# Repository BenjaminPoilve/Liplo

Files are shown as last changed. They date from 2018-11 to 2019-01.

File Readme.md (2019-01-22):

# Liplo

> You can find an article about my adventures with plotters [here](https://www.benjaminpoilve.com/projects/plotter-story.html#)

An easy-to-assemble and fun-to-use pen plotter.

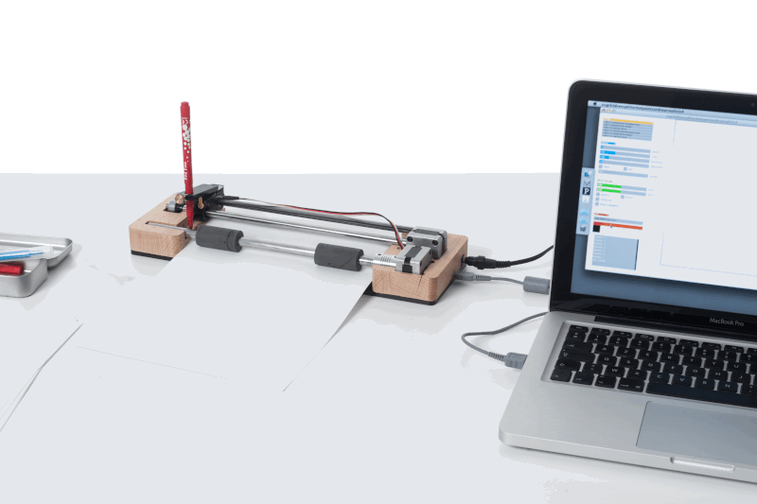
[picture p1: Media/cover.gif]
(https://www.youtube.com/watch?v=27pN25DA5TU&t=17s)


(click on the gif to have a video of all the iterations of Liplo)

The goal of this project is to imagine an easy to use and simple desktop printer, open to experimentations. Being able to use a wide array of tools (pen, pencil, brush) and paper types, it allows to really discover the world of CNC tools. Control of the printer can be done through a software that uses vector drawing, or through processing with the help of a simple software library, to discover generative drawing.

This is an old project of mine, I tried to make it a product (see my repo [LiploV2](https://github.com/BenjaminPoilve/LiploV2)) but I failed to manage the operational part of it. I put it on github in case it might inspire someone!

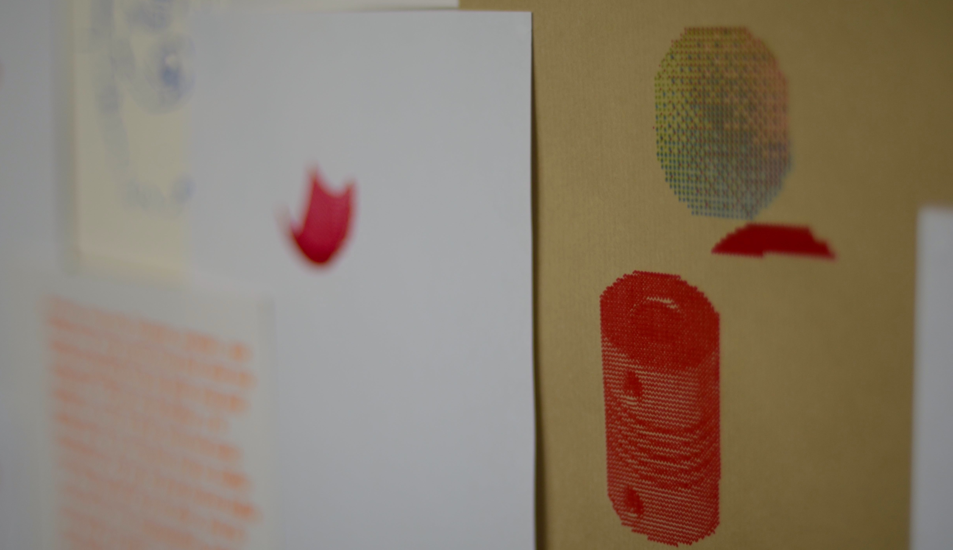
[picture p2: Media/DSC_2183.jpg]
Here

## The build

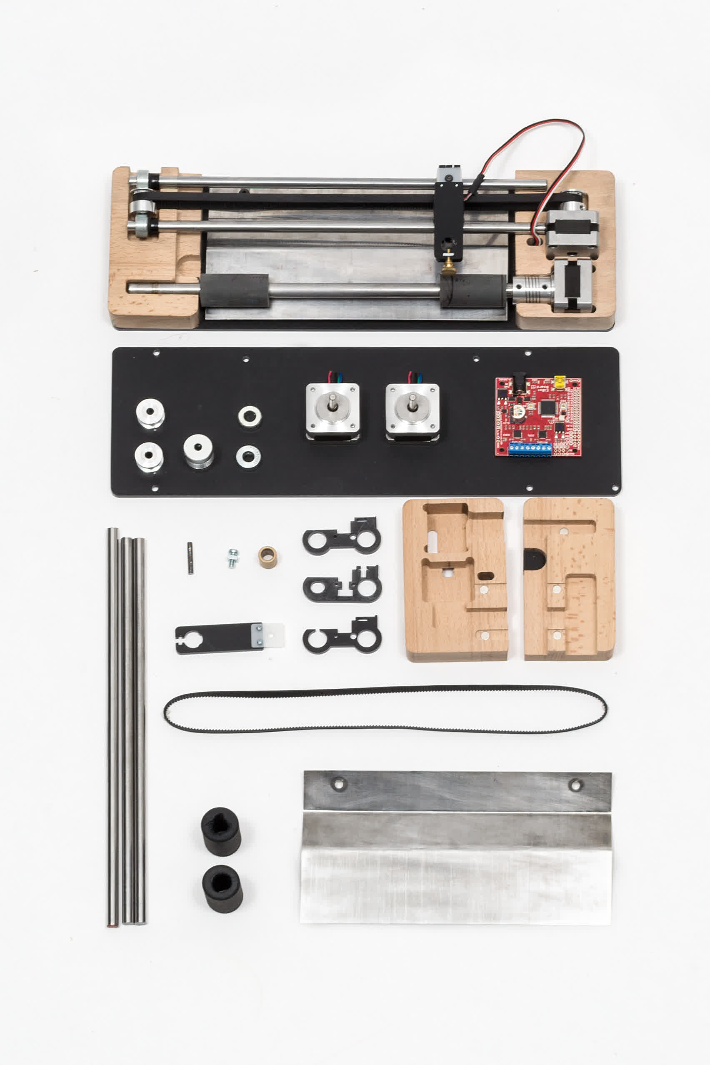
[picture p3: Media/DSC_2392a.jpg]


The construction is based on standard pieces. This allows the user to buy those pieces cheaply. 

The parts that need to be made are:

* Some laser cut parts for the head as well as the bottom of the machine
* Two CNC routed wood pieces
* A bended spring steel plate

The last one is the harder to manufacture. I did not find any manufacturer that made such parts. If you have an industrial metal bender at hand, this is pretty easy to do, but most people dont. This piece is used to maintain pressure between the paper and the roller.

On the electronic's side, I decided to use an [EibotBoard](http://www.schmalzhaus.com/EBB/). This is a very sturdy piece of hardware, that can be [bought](https://shop.evilmadscientist.com/productsmenu/188) quite cheaply. Both motor are Nema 14. I recommand [Robotdigg](https://www.robotdigg.com/) for most hardware purchase.

The last part of this project that is quite fun is that the axis are held in place only by magnet inserted in the wood. This allow for a very easy assembly.

#### B.O.M.

| Part | Approximate Price |  Link |
|---|:---:|:---:|
| EBB | $50 | [link](https://shop.evilmadscientist.com/productsmenu/188) |
| 2 Nema 14 Stepper 26mm |  $16.74|  [link](https://www.omc-stepperonline.com/nema-14-stepper-motor/nema-14-bipolar-18deg-14ncm-20ozin-04a-12v-35x35x26mm-4-wires-14hs10-0404s.html) |
| Power HD DS44 servomotor | $12 | |
| Acetal Copolymer hinge | $3.5 | [link](https://shop.evilmadscientist.com/partsmenu/200-hinges) |
| Wood | $10  | local seller  |
| Plexiglass |  $10  | local seller  |
| Flex Coupler | $1.50 |  [link](https://www.robotdigg.com/product/83/Flexible-Coupling-4mm,-5mm-Shaft-to-Screws) |
| 2 Pulley | $1.4| [link](https://www.robotdigg.com/product/226/20-Tooth-2GT-Pulley-10pcs-per-lot) |
| Linear Bearrings |  $.55 | [link](https://www.robotdigg.com/product/68/8mm-ID-Self-lubricating-Bearing)|
| GT2 Belt 6mm (not sure of length) | $1.05 | [link](https://www.robotdigg.com/product/275)|
| Tensioner| $0.15 | [link](https://www.robotdigg.com/product/41/Timing-Belt-Tensioner-Spring)|
| 2 8mm shaft collar| $0.5|  [link](https://www.robotdigg.com/product/750/DIY-motor-shaft-collar) |
| Stub 8mm| $10| local seller |
| Stub 10mm| $10 |  local seller |
| Polyurethane roller | $10 |  ebay |
| Neodyme Magnet 6mm*5mm |  $2.54 | [link](https://www.amazon.fr/Magnet-Expert-diam%C3%A8tre-n%C3%A9odyme-dadh%C3%A9rence/dp/B003MW8EJC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)|
| Spring Stell 3/10 | $5 | local seller  |
| 5*M3 screws | $1 | local seller |
| 3*M4 screws | $1 |  local seller  |
| 2 steel screws |  $1 |  local seller |

I might have forgotten a few parts but that is mostly it!

#### Laser cut parts

Two pieces are being cut in plexiglass with a laser cutter:

* The base 
* The head of the plotter

This part is inspired by Evil Mad scientist creations. This uses the same flexible hinge/servo association to lift the pen. 

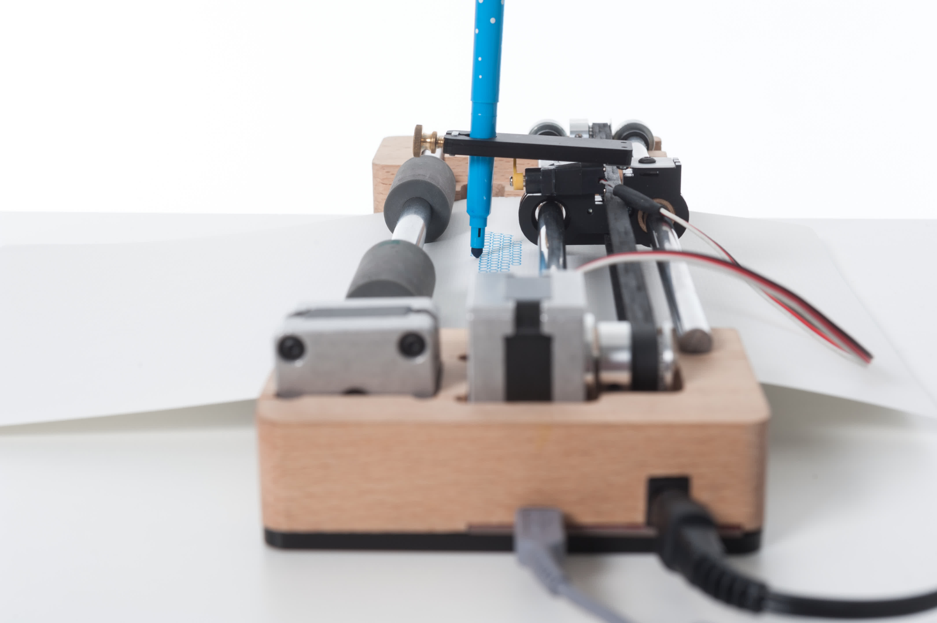
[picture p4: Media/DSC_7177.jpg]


There are three laser cut parts that assemble together and that clamp the timing belt. 

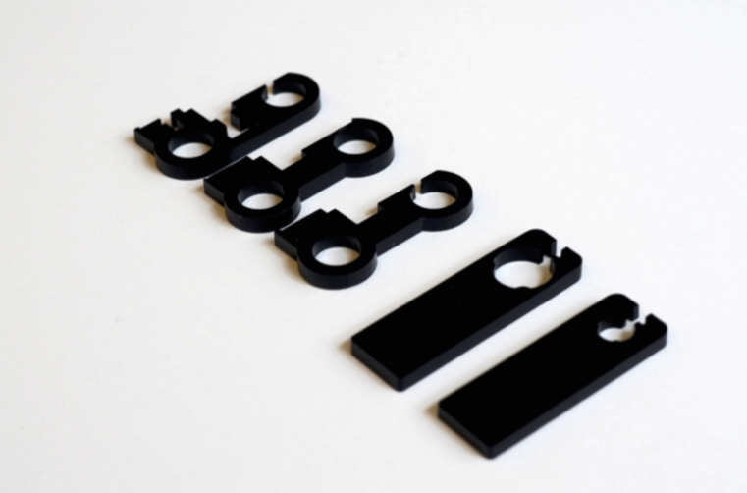
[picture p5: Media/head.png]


All the part can be cut from the same plexiglass stock.

See [here](Hardware/Plans/LaserCutParts)

#### CNC routed parts

For the routed parts, I choose to generate the gcode from a 2D drawing and not a 3D one. The goal was to have only one tool (6mm router head) for all the cutting, and to optimise the router path 

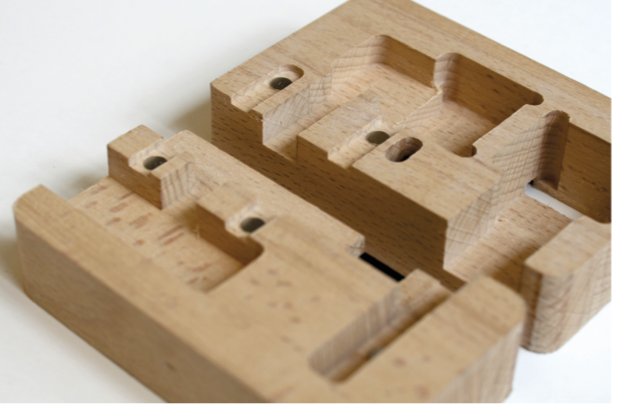
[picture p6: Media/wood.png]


What's more, since I did not have access to a very sophisticated router, I choose to use something that I call a flip cut to handle the part flip during routing.

The main idea is to have a border cut that allows the piece to be hold when the flip has been made.

It looks like this:

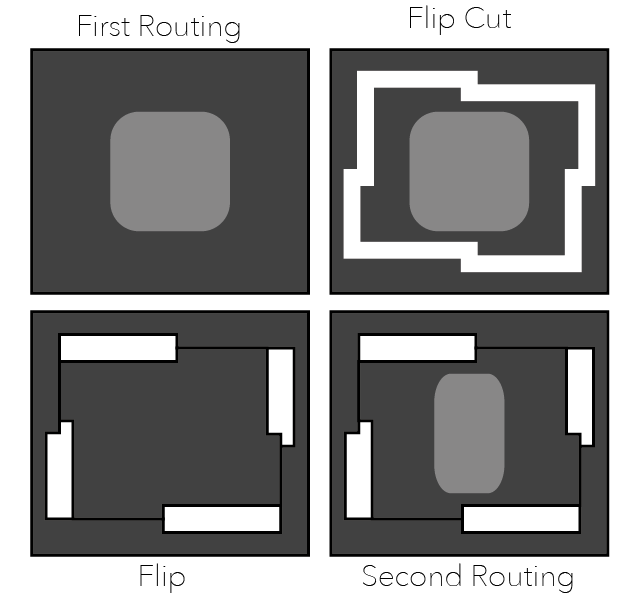
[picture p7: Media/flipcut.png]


You can find the G-code [here](Hardware/Plans/CNCparts) as well as the drawing you would need to regenerate the G-code.

## The software

The board itself already has an EibotFirmware.

Regarding the host computer, I made, using Processing (that was a long time ago!), a sender software.

#### Sender software

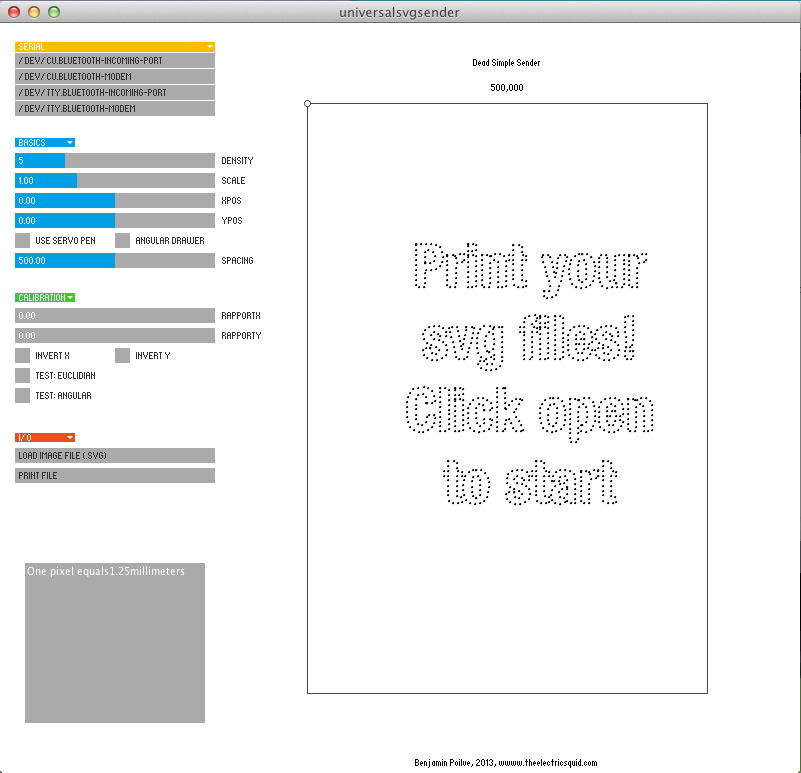
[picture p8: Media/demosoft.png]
(https://drive.google.com/file/d/0BxsBFm8YwdRAMFMyQm1iZnZlT28/view?usp=sharing)


(click image for video)

This software made with processing has the following features:

* Easy connection to the Eibotboard
* Supports SVG file
* Supports multiple colors files, with tool change
* Allows for easy choice of speed and polygonalisation density
* Allows for live visualisation of the drawing
* Allows to pause/resume jobs.

You can find a macOs version of the software [here](https://github.com/BenjaminPoilve/Liplo/releases)

#### The library

The main idea was to have an easy class to instantiate in processing to allow generative drawing experiment.

You can find the class [here](https://github.com/BenjaminPoilve/Liplo/blob/master/Software/Sender/Plot2.pde).

It never made it into a proper library, but the usage would be:

```
  plotter = new Plot2(this);
  int val=2 //the serial port number
  plotter.openport(val);
  plotter.line(10,10,20,20)
  plotter.ellipse(20,20,10,10,10)

```

The coding style is poor, and it was mostly trial and error, but I really loved the idea of easily test some generative drawing. Even to explain for loops to kids, this proved to be a useful tool, and having a real-world result of your program really helps to keep them engaged in the activity. So, food for thoughts, but no real library.

### Conclusion

I really hope this will inspire people to build their own, and start playing with it! 

I really loved doing this project, and even got a few "maker of merit" price for it at the Paris MakerFaire!

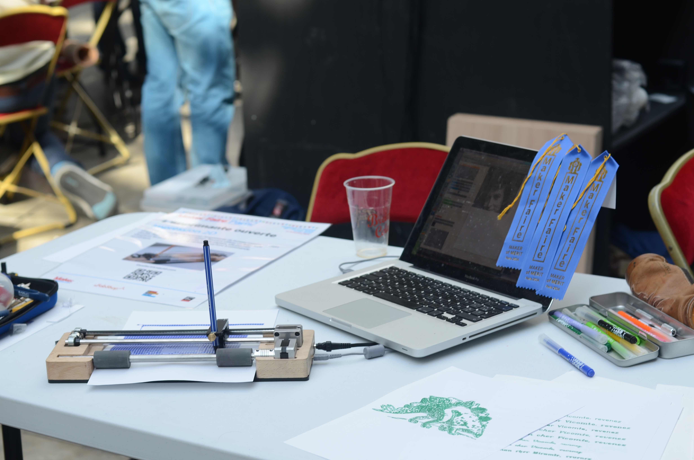
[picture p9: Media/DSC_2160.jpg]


### Caveats

* Newest processing version does not run the program. Some tweaking might be needed to adapt it
* The stepper get hot! Especially after a while. This is an usual feature (working temp is aroung 80°) but still is an issue, especially with kids.
* I never packaged the processing library. Bad me.

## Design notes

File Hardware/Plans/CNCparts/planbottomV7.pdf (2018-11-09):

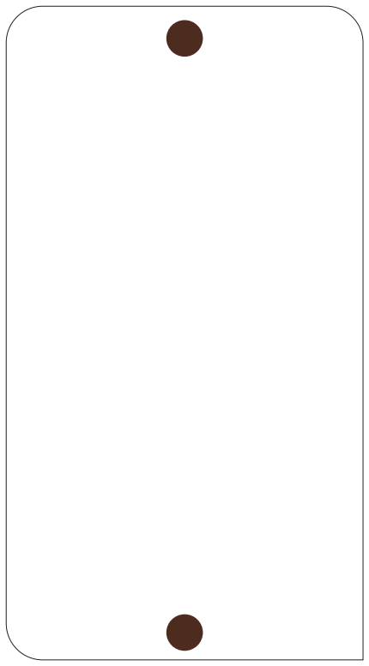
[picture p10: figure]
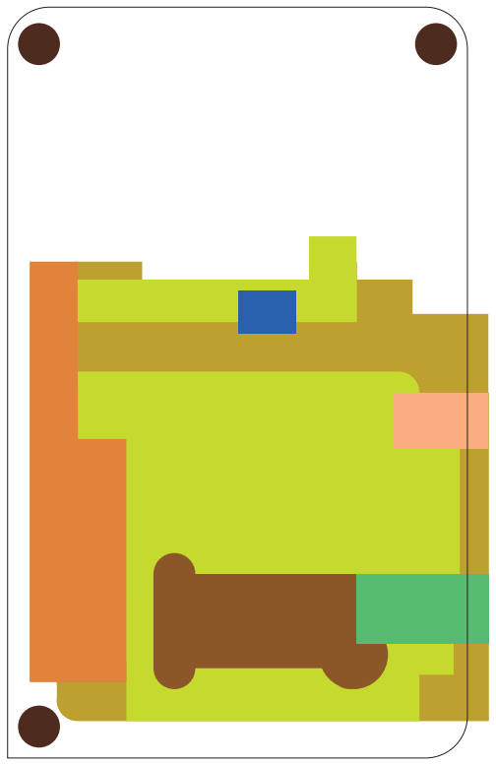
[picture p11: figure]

11.4

12.9

13.9

5.4

2.8

11

7

6.7

Traversant

22.3

Distance en mm à partir de la surface de travail- Epaisseur: 25mm

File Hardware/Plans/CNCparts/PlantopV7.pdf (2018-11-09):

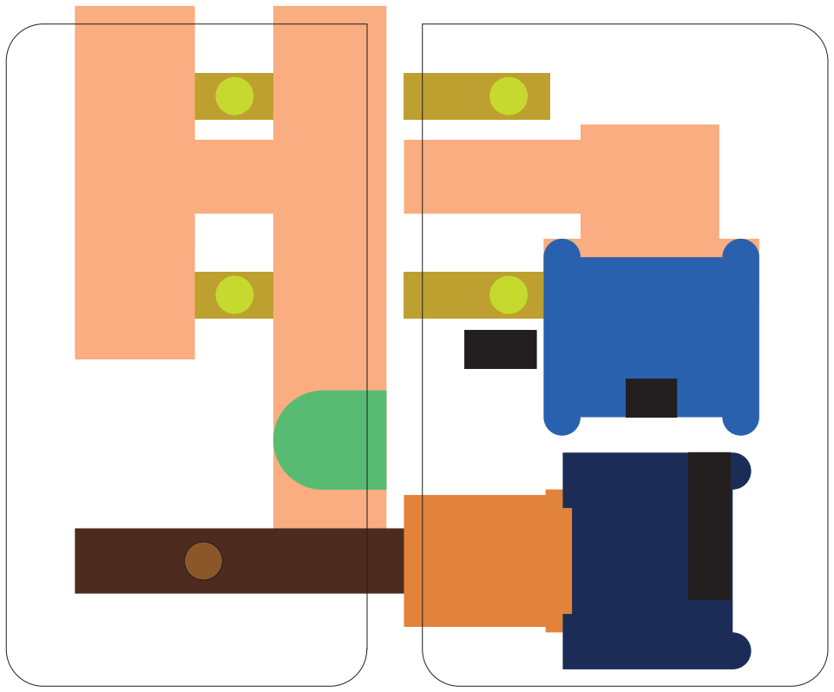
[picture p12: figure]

15.4

16

19.8

7

1.9

14.8

9.9

9.1

Traversant

22.3

Distance en mm à partir de la surface de travail- Epaisseur: 25mm

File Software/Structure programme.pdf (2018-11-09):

## Plotter

Gère la communication avec le traceur, la connection, lʼenvoie de donnée et regroupe un ensemble de fonction de base comme le réglage de la vitesse, le levé ou baissé de stylo, le tracage de point, dʼellipse, de ligne, le comptage de la distance parcourue ( en cas de pinceaux)..
Toute ces fonctions sont interfacées pour pouvoir etre facilement utilisée dans le reste du programme (ex: plotter.penUp() leve le stylo)

(Classe)

## Loop

Fonction de tracacage principale. A partir du premier point de la couleur demandée à tracer, envoie au fur et a mesure les points à la fonction plot. Quand le numéro de point correspond à la fin de la couleur, se remet en attente

(Fonction)

Utilise: Processing serial Lib

## File UI

Ouvre un selecteur de fichier qui permet de charger un fichier en passant par le naviguateur de dossier de lʼOS de lʼutilisateur. Passe le fichier à la fonction qui lʼa appelé après avoir verifié que le type de fichier correspond bien

(Fonction)

Demande dʼimpression | Demande dʼouverture fichier

Processing
http://en.wikipedia.org/wiki/Processing_%28programming_language%29#License
Java
http://fr.wikipedia.org/wiki/Java_et_logiciel_libre#Licence_n.C2.B01.21
Geomerative
http://www.ricardmarxer.com/old_geomerative/documentation/
ControlP5
https://code.google.com/p/controlp5/

Utilise

Appelle

Demande connection machine

Demande de tracé

Appelle

Appelle

Utilise

Utilise

Utilise: Java.swing Jfilechooser

## SVG reader

Met le fichier SVG à la bonne echelle, le polygonalise

(Classe)

Utilise: Geomerative

## Exvert

Parcourt de manière récursive lʼensemble des points du fichier svg et les enregistre dans un tableau de point avec leurs attributs ( couleurs, numéro de forme, épaisseur du trait)

(Fonction)

Utilise: Geomerative

## Points

Structure de donnée qui permet de stocker les points et leurs attributs. Contient un algorithme de classement des points selon leur couleur.

(Classe)

Utilise: Java.util Collection

## Plot

Recoit un numéro de point. Identifie si le point est un début, milieu ou fin de tracé, demande à lʼimprimante de bouger en fonction et dʼactionner ou pas le stylo. Si besoin, trace le trait correspondant au tracé effetué à lʼecran.

(Fonction)

Utilise: -

## Find color end/start

Trouve dans la structure de donnée points le point de depart et de fin de chaque couleur de tracé.

(Fonction)

Utilise: -

Utilise: -

## Début programme

Initialise lʼinterface et met en place les eventHandlers qui vont appeler les autres fonctions en cas dʼevenement utilisateur

(Fonction)

Utilise: ControlP5

Utilise

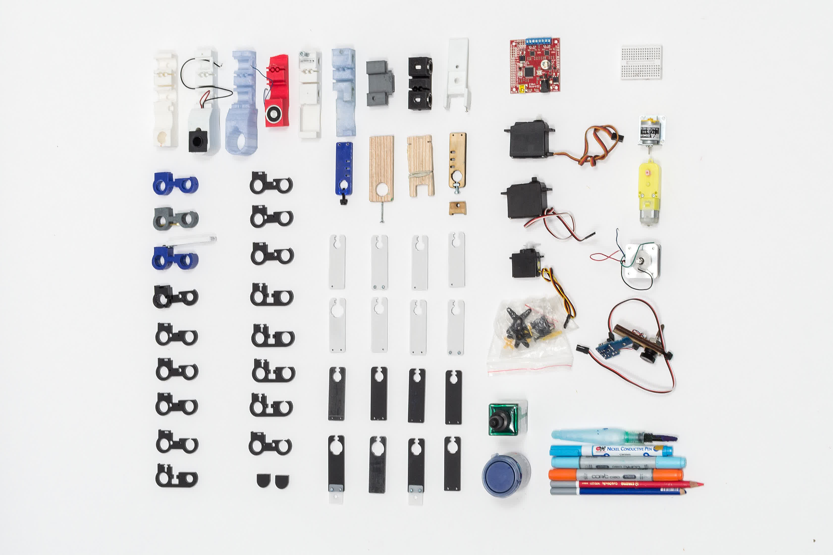
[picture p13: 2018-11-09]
Media/DSC_2387a.jpg

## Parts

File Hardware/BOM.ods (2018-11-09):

Produit | Quantité | Prix unitaire(m,m^2) | Prix total |  | Source
Stepper Nema 14 | 2 | 7,145 | 14,29 |  | http://www.omc-stepperonline.com/stepper-motors-nema-14-stepper-motors-c-1_34.html
Hetre massif 26mm | 0,025 | 350 | 8,75 |  | Azbois
EBB | 1 | 36,569 | 36,569 |  | https://www.sparkfun.com/products/10025
Plexiglass noir mat 5mm | 0,068 | 80 | 5,44 |  | Weber (verif prix)
Flex coupler | 1 | 1,318 | 1,318 |  | RobotDigg
Pulley | 2 | 1,53 | 3,06 |  | RobotDigg
Roulement lineaire | 1 | 0,43 | 0,43 |  | RobotDigg
Belt GT2 6mm | 1 | 2,123 | 2,123 |  | RobotDigg
Stub 8mm | 0,5 | 21 | 10,5 |  | Weber (verif prix)
Aimant Neodyme 6*5 | 5 | 0,3 | 1,5 |  | Magnetshop
Tole Ressort 3/10 | 0,25 | 20 | 5 |  | Weber (verif prix)
Stub 10mm | 0,28 | 35 | 9,8 |  | Weber (verif prix)
Servo PowerHD ds44 | 1 | 14,4 | 14,4 |  | Euromodel
Visserie(5*M3,3*M4,4*vis tole,2boulon,vis molette) | 1 | 5 | 5 |  | Vis Champion
Lamelle acetal copolymere | 0,0002 | ? |  |  | Weber (verif prix)
Laser(temps) | 3 | 1 | 3 |  | estimation a 1 euro la minute de temps machine
Usinage (temps) | 15 | 1 | 15 |  | estimation a 1 euro la minute de temps machine
Assemblage (temps) | 10 | 0,15 | 1,5 |  | estimation de l'ordre du smic
Pliage tole |  |  |  |  | a trouver prestataire
 |  |  | Total | 137,68

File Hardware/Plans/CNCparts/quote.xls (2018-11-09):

 |  |  |  |  | TELECOPIE
 |  |  |  |  |  |  |  | PERIGNAC LE: | 2014-10-28
SARL au capital de 7.700 € |  |  |  | DESTINATAIRE |  | BENJAMIN POILVE | N° TELECOPIE
RCS Saintes 438 115 768 |  |  |  | SOCIETE |  |  | N° TELEPHONE
PREROUX |  |  |  | EXPEDITEUR |  | P.GUILLET |  | benjamin.poilve@centraliens.net
17800 PERIGNAC |  |  |  | OBJET | REMISE DE PRIX
Tél: 05.46.94.08.52 Port:06.74.68.04.37.
actibois17@wanadoo.fr
MESSAGE : |  | REF: | ENBOUT
 |  | MATIERE: |  | HETRE MASSIF LAMELLE COLLE
 |  | DIMENTIONS: |  | 76 X 66 X 25 ET 76 X 59X 25
 |  | USINAGES : |  | 2FACES
 |  | FINITION: |  | BRUTE
 |  | QANTITE: |  | 500
 |  | FINITION: |  | VERNIE
 |  | QANTITE: |  | 500 |  | 16.70 €
 |  | PRIX PROTO X 3
 |  | PRIX PIECE HT DEPART PERIGNAC
 | LES PRIX INDIQUES SUR CETTE OFFRE RESTENT VALABLES PENDANT 2 MOIS.
 | TOUTES MODIFICATIONS APPORTEES FERONT L'OBJET D'UNE NOUVELLE OFFRE DE PRIX.
 | DELAI DE REALISATION 4 A 5 SEMAINES A RECEPTION DE MATIERE.
 | REGLEMENT DE PRESTATION A LA COMMANDE.
 | EN ESPÉRANT QUE CES PRIX RETIENDRONT VOTRE ATTENTION JE RESTE A VOTRE DISPOSITION
 | POUR TOUT RENSEIGNEMENT COMPLÉMENTAIRE.
 |  |  | SALUTATIONS
 |  |  | P.GUILLET

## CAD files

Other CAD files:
Hardware/Plans/CNCparts/planbottomV7.dxf
Hardware/Plans/CNCparts/PlantopV7.dxf

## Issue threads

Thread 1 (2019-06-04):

Hot stepper motors? Try this

Ianmcmill, 2019-06-04:
You use 12v stepper motors. Try motors which are spec'd at 3 to 4v.
Those 12v stepper motors are inappropriate for 3d printers/plotters etc.
I have a bunch of 12v steppers and they collect dust in my shelf because they get too hot. Adjusting current on the driver board does not help here. Their resistance is way too high (30ohms)
4v steppers have around 7ohms which is why they don't get so hot.

BenjaminPoilve, 2019-06-04:
Thanks for the input!

My physics must be a little rusty, but if the torque is proportionnal to the input watt-age, to get an equivalent wattage at lower resistance I would need to pump more Intensity (W=UxI) which would creat much more heat as intensity is squared in Joules' Law (P ~RI^2). So for equivalent torque, wouldn't there be more heat?

I think the crux of the problem is that stepper are always overpowered to avoid any potentiel step losses, which leads to overheating. Most of the 3D printer I've seen use 12 or 24v steppers, which run pretty hot (~80°c)..

Ianmcmill, 2019-06-04:
All physics aside. My 3d printer steppers are rated 2.0A 3.6V. Okay not quiet 0.4A. Nevertheless.
I have never had any steppers rated above 4V in the datasheets.
They are driven by a A4988 with the voltage set to **0.6V** using the potentiometer of the driver. They barely get 35°C. The torque is good. Not loosing steps. Same on my polargraph. I have a hard time pulling the belt to get it into home position when the motors are powered.
If they would reach 80°C my PLA parts would warp and sag.

https://www.omc-stepperonline.com/de/nema-17-bipolar-59ncm-84oz-in-2a-42x48mm-4drahte-w-1m-kabel-and-verbinder.html
The less resistance the coils have, the cooler.

Ianmcmill, 2019-06-04:
And I forgot one thing. Your Liplo plotter is a really nice designed machine!

BenjaminPoilve, 2019-06-05:
Well, my (possibly flawed) understanding of physica always prevented me from trying such low voltage steppers! I'll sure give it a try in my next project. Thanks for the insight, any idea why such a faulty design is so common? I have had both makerbot and printrbot printer and I am pretty sure both use 12v motors and are prone to overheating!
To avoid the issue I tried using sensored DC motors, but at the pricepoint I wanted to attain, the motors were much to fragile.
Thanks for the compliment, it means a lot!

Ianmcmill, 2019-06-25:
I jst realized a thing about my steppers and my driver. I think this is important to add to this topic.
I measured the Vref on my drivers and I did set them so that the stepper motors run at around 40% of their rated current. I have had no problems with losing steps. Even on my 3D printer.
I found this out when I used this calculator https://v6zmvq5nk5.codesandbox.io/ and adjusted my steppers accordingly. They became very hot. Then I decreased the Vref again down to a point where the motors had enough torque to move the X and Y gantry and didn't lose steps.

On a plotter like yours, where even less mass has to be moved (no extruder/hotend) you could also go down to maybe 30% of the rated current.
As I said, my 3D printer runs fine with 40%.

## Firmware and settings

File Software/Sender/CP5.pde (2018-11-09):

import controlP5.*; 
import javax.swing.UIManager; 
import javax.swing.JFileChooser; 
import java.util.Collections;
ControlP5 controlP5;
Println console;
Slider[] sliders;
Range[] ranges;
Toggle[] toggles;
Bang[] bangs;



int invertx=-1;
  int inverty=-1;
  float gox=0;
  float goy=0;

boolean paused=false;
boolean quitting=false;
//other info
int drawingxcenter;
int drawingycenter;
int drawingheight;
int drawingwidth;
int left = 0;
int top = 5;
int len = 200;

void controlp5init() {

     color activeColor = color(100);
  controlP5 = new ControlP5(this);
  controlP5.setAutoDraw(false);
  controlP5.setColorActive(activeColor);
  controlP5.setColorBackground(color(170));
  controlP5.setColorForeground(color(100));
  controlP5.setColorLabel(color(50));
  controlP5.setColorValue(color(255));


  Textarea myTextarea = controlP5.addTextarea("txt")
    .setPosition(25, 500)
      .setSize(180, 130)
        .setFont(createFont("", 10))
          .setLineHeight(14)
            .setColor(color(255))
              .setColorBackground(color(170, 170, 170))
                .setColorForeground(color(170, 100));
  ;

  console = controlP5.addConsole(myTextarea);//

  sliders = new Slider[30];
  ranges = new Range[30];
  toggles = new Toggle[30];
  bangs = new Bang[30];



  int si = 0;
  int ri = 0;
  int ti = 0;
  int bi = 0;
  int posY = 0;


  int left = 0;
  int top = 5;
  int len = 200;
  ListBox listBox = controlP5.addListBox("Serial")
    .setPosition(15, 30)
      .setSize(200, 200)
        .setItemHeight(10)
          .setBarHeight(10)
            .setColorBackground(color(252, 188, 0))
              .setColorActive(color(252, 188, 0))
                .setColorLabel(color(255))
                  ;

  String[] ports = Serial.list();
  println(ports);
  for (int i=0; i<ports.length; i++) {
    ListBoxItem lbi=listBox.addItem(ports[i], i);
    lbi.setColorBackground(color(170));
    lbi.setColorForeground(color(252, 188, 0));
    lbi.setColorLabel(color(50));
    lbi.setColorActive(color(252, 188, 0));
  }





  int oldsi=si;
  int oldri=ri;
  int oldti= ti;
  int oldbi=bi;

  ControlGroup ctrl2 = controlP5.addGroup("Basics", 15, 125, 60);
  ctrl2.activateEvent(true);
  ctrl2.setColorLabel(color(255, 255, 255));
  ctrl2.activateEvent(true);
  ctrl2.setColorBackground(color(0, 159, 227));
  ctrl2.open();

  top=5;
  posY=0;

  sliders[si++] = controlP5.addSlider("Density", 0, 20, left, top+posY, len, 15)
    .setValue(float(1));
    
   

  sliders[si++] = controlP5.addSlider("Scale", 0.1, 3, left, top+posY+20, len, 15)
    .setValue(1);
  sliders[si++] = controlP5.addSlider("SeekSpeed", 0.1,10, left, top+posY+40, len, 15)
    .setValue(float(2));
  sliders[si++] = controlP5.addSlider("DrawSpeed",  0.1,10, left, top+posY+60, len, 15)
    .setValue(float(1));
  toggles[ti] = controlP5.addToggle("Pause", left+0, top+posY+80, 15, 15);
  toggles[ti++].setLabel("Pause");
  posY += 80;




  toggles[ti] = controlP5.addToggle("Quit",  left+100, top+posY, 15, 15);
  toggles[ti++].setLabel("Quit");
  sliders[si++] = controlP5.addSlider("Spacing", 1, 1000, left, top+posY+20, len, 15)
    .setValue(1);

  posY += 70;



  for (int i = oldsi ; i < si; i++) {
    sliders[i].setGroup(ctrl2);
    sliders[i].captionLabel().toUpperCase(true);
    sliders[i].captionLabel().style().padding(4, 3, 3, 3);
    sliders[i].captionLabel().style().marginTop = -4;
    sliders[i].captionLabel().style().marginLeft = 0;
    sliders[i].captionLabel().style().marginRight = -14;
    sliders[i].captionLabel().setColorBackground(0x99ffffff);
    sliders[i].setColorForeground(color(0, 159, 227));
  }
  for (int i = oldri; i < ri; i++) {
    ranges[i].setGroup(ctrl2);
    ranges[i].captionLabel().toUpperCase(true);
    ranges[i].captionLabel().style().padding(4, 3, 3, 3);
    ranges[i].captionLabel().style().marginTop = -4;
    ranges[i].captionLabel().setColorBackground(0x99ffffff);
  }
  for (int i = oldti; i < ti; i++) {
    toggles[i].setGroup(ctrl2);
    toggles[i].setColorLabel(color(50));
    toggles[i].captionLabel().style().padding(4, 3, 3, 3);
    toggles[i].captionLabel().style().marginTop = -20;
    toggles[i].captionLabel().style().marginLeft = 18;
    toggles[i].captionLabel().style().marginRight = 5;
    toggles[i].captionLabel().setColorBackground(0x99ffffff);
    toggles[i].setColorActive(color(0, 159, 227));
    sliders[i].setColorForeground(color(0, 159, 227));
  }
  for (int i = oldbi; i < bi; i++) {
    bangs[i].setGroup(ctrl2);
    bangs[i].setColorLabel(color(50));
    bangs[i].captionLabel().style().padding(4, 3, 3, 3);
    bangs[i].captionLabel().style().marginTop = -20;
    bangs[i].captionLabel().style().marginLeft = 48;
    bangs[i].captionLabel().style().marginRight = 5;
    bangs[i].captionLabel().setColorBackground(0x99ffffff);
  }



  oldsi=si;
  oldri=ri;
  oldti= ti;
  oldbi=bi;

  ControlGroup ctrl3 = controlP5.addGroup("Calibration", 15, 280, 60);
  ctrl3.activateEvent(true);
  ctrl3.setColorLabel(color(255, 255, 255));
  ctrl3.activateEvent(true);
  ctrl3.setColorBackground(color(50, 205, 50));
  ctrl3.open();
  top=5;
  posY=0;

  sliders[si++] = controlP5.addSlider("MoveX", -50, 50, left, top+posY, len, 15)
   .setValue(float(0));
  sliders[si++] = controlP5.addSlider("MoveY", -50, 50, left, top+posY+20, len, 15)
   .setValue(float(0));
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

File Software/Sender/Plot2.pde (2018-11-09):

import processing.serial.*;

class Plot2 {
  PApplet parent;
  // variables for serial connection to EiBotBoard
  Serial myPort;
  int portnum;  // Create object from Serial class
  int val;        // Data received from the serial port
  int deltax=0;
  int deltay=0;
  boolean pen;
  float oldx=0;
  float oldy=0;
  
  float checksumx=0;
  float checksumy=0;
  boolean refill;
  float posx=0;
  float decal=10;
  float posy=0;
  float drawspeed=1;
  float seekspeed=2;
  //test write output flags
  boolean writeToConsole = false;      //true will write only to console, not to EiBotBoard
  PMatrix matrix;

  Plot2(PApplet parenting) {
    matrix = parenting.getMatrix();
    // setup serial port
    parent=parenting;
    
  }

  //used to convert between machine coordinates and paper coordinates

  void openport(int portnum){
   
    try {
      String portName = Serial.list()[portnum];
      println(portName);
      myPort = new Serial(parent,portName, 9600);
      //serial device found
      println("found: " + portName);
      println("Plotter Online");
      println("ready to roll!");
      connected=true;
       if (!writeToConsole) myPort.write( "SC,4,10000 \r");
    if (!writeToConsole) myPort.write( "SC,5," + 18000 + "\r");
    // sendCommand( "SC,10," + min(_servoRateUp,_servoRateDown) + "\r");
    if (!writeToConsole) myPort.write( "SC,11," +2000+ "\r");
    if (!writeToConsole) myPort.write( "SC,12," + 2000+ "\r");
    String outConsole = ("SM,"+500+","+0+","+(-500)+"\r"); //SP,<value>,<duration> : <value> is 0 (for up) or 1 (for down)
    if (!writeToConsole) myPort.write(outConsole);


    penUp();
    } 
    catch (Exception e) {
      //no serial device found
      println("Didn't find Plotter");
      println(e);
      writeToConsole = true;
    }
   
  }
    
    
    
    
    
    
    
    
    
    
    
  


  void goingto(float x, float y, float intensity) {
    float[] out = new float[2];
    float[] vec = new float[2];
    vec[0] = x;
    vec[1] = y;
    getMatrix().mult(vec, out);
    x=out[0];
    y=out[1];
    int pasx=int((x-oldx)*80.6);
    int pasy=int((y-oldy)*45);
    
    // println(checksumx/50.0-x);
    // println(checksumy/25.0-y);
    if (pen==true) {
      deltax+=abs(pasx);
      deltay+=abs(pasy);
    }
    println("Go to x "+pasx+" y "+pasy);
    float distance=sqrt((pow(pasx, 2)+pow(pasy*2, 2)));
    if (distance!=0) {
      float vitesse=drawspeed;
      if (pen==false ) {
        vitesse=seekspeed;
      }
      if (vitesse>10 ) {
        vitesse=10;
      }
      if (intensity!=0 ) {
        vitesse=intensity;
      }


      int towait=int(distance/vitesse)+10;
      // println(towait);

      String outConsole = ("SM,"+towait+","+inverty*pasy+","+invertx*pasx+"\r"); //SP,<value>,<duration> : <value> is 0 (for up) or 1 (for down)
      if (!writeToConsole) myPort.write(outConsole);

      delay(int(towait));
    }
    oldx=oldx+float(pasx)/80.6;
    oldy=oldy+float(pasy)/45;
    if (deltax+deltay>10000) {
      deltax=0;
      deltay=0;
      refill=true;
    }
    posx=x;
    posy=y;
  }



  void goingtoabsolute(float x, float y, float intensity) {

    x=x;
    y=y;
    int pasx=int((x-oldx)*80.6);
    int pasy=int((y-oldy)*45);
    checksumx+=pasx;
    checksumy=pasy;
    // println(checksumx/50.0-x);
    // println(checksumy/25.0-y);
    if (pen==true) {
      deltax+=abs(pasx);
      deltay+=abs(pasy);
    }
    println("Go to x "+pasx+" y "+pasy);
    float distance=sqrt((pow(pasx, 2)+pow(pasy*2, 2)));
    if (distance!=0) {
      float vitesse=seekspeed;
      if (vitesse>10 ) {
        vitesse=10;
      }
      if (intensity!=0 ) {
        vitesse=intensity;
      }

      int towait=int(distance/vitesse)+10;
      // println(towait);

      String outConsole = ("SM,"+towait+","+inverty*pasy+","+(invertx*pasx)+"\r"); //SP,<value>,<duration> : <value> is 0 (for up) or 1 (for down)
      if (!writeToConsole) myPort.write(outConsole);

      delay(int(towait));
    }
    oldx=oldx+float(pasx)/80.6;
    oldy=oldy+float(pasy)/45;
    if (deltax+deltay>10000) {
      deltax=0;
      deltay=0;
      refill=true;
    }
    posx=x;
    posy=y;
  }




  void gogetink(float ysec, float y, float xsec) {

    goingto(0, y, 0);
    penDown();
    delay(500);
    penUp();
    goingto(xsec, ysec, 0);
  }
  void penDown() {
    //pen down
    pen=true;
    println("pen down");
    String outConsole = ("SP,1,100\r"); //SP,<value>,<duration> : <value> is 0 (for up) or 1 (for down)
    if (!writeToConsole) myPort.write(outConsole);
    delay(200);
  }

  void penUp() {
    //pen up
    pen=false;
    println("pen up");
    String outConsole = ("SP,0,100\r"); //SP,<value>,<duration> : <value> is 0 (for up) or 1 (for down)
    if (!writeToConsole) myPort.write(outConsole);
    delay(200);
  }
  
   void Toggle() {
    if(pen==true){
            penUp();
          }else{
            penDown();}
              
  }

  void shutDown() {
    String outConsole = ("EM,0,0\r");
    if (!writeToConsole) myPort.write(outConsole);
    println("shut down");
  }

  void goHome() {
    goingto(0, 0, 0);
  }


  void gotofirstpoint(float x, float y) {
    // println("goy"+posy+"aim"+y);
    //  println("gox"+posx+"aim"+x);
    float dist=sqrt(pow(x-posx, 2)+pow(y-posy, 2));
    if (dist>0) {

      penUp();
      goingto(x, y, 0);
      penDown();
    }
    if (pen==false) {
      penDown();
    }
  }


  void line(float x, float y, float xaim, float yaim) {
    gotofirstpoint(x, y);
    goingto(xaim, yaim, 0);
  }

  void point(float y, float x) {
    gotofirstpoint(x, y);
  }


  void ellipse(float x, float y, float widthell, float heightell, int def) {
    gotofirstpoint(x+widthell/2.0, y);

    for (int i=0; i<=def;i++) {
      goingto(x+ widthell/2.0*cos(i/float(def)*2*PI), y+heightell/2.0*sin(i/float(def)*2*PI), 0);
      fill(255, 0, 0);
    }
  }

  void rect(float y, float x, float widthrect, float heightrect) {
    gotofirstpoint(x, y);
    goingto(x+widthrect, y, 0);
    goingto(x+widthrect, y+heightrect, 0);
    goingto(x, y+heightrect, 0);
    goingto(x, y, 0);
  }

  void setDrawspeed(float speed) {

    drawspeed=speed;
   
   println("drawspeed "+speed);
  }
  
  void setSeekspeed(float speed) {

    seekspeed=speed;
      println("seekspeed "+speed);
  }

  void onquit() {
    penUp();
    goingtoabsolute(0, 0, 0);
    String outConsole = ("SM,"+500+","+0+","+(1600)+"\r"); //SP,<value>,<duration> : <value> is 0 (for up) or 1 (for down)
    if (!writeToConsole) myPort.write(outConsole);
    shutDown();
    myPort.clear();
      // Close the port
      myPort.stop();
  }
  
  void coordrez(){
    oldx=0;
    oldy=0;
  }
    
  
  
  void moveX(float x) {
 int pasx=int((x-oldx)*80.6);
  println("Go to x "+pasx);
    float distance=abs(pasx);
    if (distance!=0) {
      float vitesse=drawspeed;
      if (pen==false ) {
        vitesse=seekspeed;
      }
      if (vitesse>10 ) {
        vitesse=10;
      }
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
